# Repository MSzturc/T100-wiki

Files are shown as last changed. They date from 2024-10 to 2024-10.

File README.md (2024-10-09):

<p align="center">
  <a href="https://getdoks.org/">
    Doks
  </a>
</p>

<h1 align="center">
  Doks
</h1>

<h3 align="center">
  Modern Documentation Theme
</h3>

<p align="center">
  Doks is a Hugo theme for building secure, fast, and SEO-ready documentation websites, which you can easily update and customize.
</p>

<p align="center">
  <a href="https://github.com/h-enk/doks/blob/master/LICENSE">
    
  </a>
  <a href="https://github.com/h-enk/doks/releases">
    
  </a>
  <a href="https://www.npmjs.com/package/@hyas/doks">
    
  </a>
  <a href="https://github.com/h-enk/doks/actions?query=workflow%3A%22Hyas+CI%22">
    
  </a>
  <a href="https://app.netlify.com/sites/doks/deploys">
    
  </a>
</p>

Doks — Modern Documentation Theme

## Demo

- [doks.netlify.app](https://doks.netlify.app/)

## Why Doks?

Nine main reasons why you should use Doks:

1. __Security aware__. Get A+ scores on [Mozilla Observatory](https://observatory.mozilla.org/analyze/doks.netlify.app) out of the box. Easily change the default Security Headers to suit your needs.

2. __Fast by default__. Get 100 scores on [Google Lighthouse](https://googlechrome.github.io/lighthouse/viewer/?gist=59aafe464a68f8bc30b8e9a636d5b053) by default. Doks removes unused css, prefetches links, and lazy loads images.

3. __SEO-ready__. Use sensible defaults for structured data, open graph, and Twitter cards. Or easily change the SEO settings to your liking.

4. __Development tools__. Code with confidence. Check styles, scripts, and markdown for errors and fix automatically or manually.

5. __Bootstrap framework__. Build robust, flexible, and intuitive websites with Bootstrap 5. Easily customize your Doks site with the source Sass files.

6. __Netlify-ready__. Deploy to Netlify with sensible defaults. Easily use Netlify Functions, Netlify Redirects, and Netlify Headers.

7. __Full text search__. Search your Doks site with FlexSearch. Easily customize index settings and search options to your liking.

8. __Page layouts__. Build pages with a landing page, blog, or documentation layout. Add custom sections and components to suit your needs.

9. __Dark mode__. Switch to a low-light UI with the click of a button. Change colors with variables to match your branding.

### Other features

- __Multilingual and i18n__ support
- __Versioning__ documentation support
- __KaTeX__ math typesetting
- __Mermaid__ diagrams and visualization
- __highlight.js__ syntax highlighting

## Requirements

- [Git](https://git-scm.com/) — latest source release
- [Node.js](https://nodejs.org/) — latest LTS version or newer

<details>
<summary>Why Node.js?</summary>

Doks uses npm (included with Node.js) to centralize dependency management, making it [easy to update](https://getdoks.org/docs/help/how-to-update/) resources, build tooling, plugins, and build scripts.

</details>

## Get started

Start a new Doks project in three steps:

### 1. Create a new site

Doks is available as a child theme and a starter theme.

#### Child theme

- Intended for novice to intermediate users
- Intended for minor customizations
- [Easily update npm packages](https://getdoks.org/docs/help/how-to-update/) — __including__ [Doks](https://www.npmjs.com/package/@hyas/doks)

```bash
git clone https://github.com/h-enk/doks-child-theme.git my-doks-site && cd my-doks-site
```

#### Starter theme

- Intended for intermediate to advanced users
- Intended for major customizations
- [Easily update npm packages](https://getdoks.org/docs/help/how-to-update/)

```bash
git clone https://github.com/h-enk/doks.git my-doks-site && cd my-doks-site
```

<details>
<summary>Help me choose</summary>

Not sure which one is for you? Pick the child theme.

</details>

### 2. Install dependencies

```bash
npm install
```

### 3. Start development server

```bash
npm run start
```

## Other commands

Doks comes with [commands](https://getdoks.org/docs/prologue/commands/) for common tasks.

## Documentation

- [Netlify](https://docs.netlify.com/)
- [Hugo](https://gohugo.io/documentation/)
- [Doks](https://getdoks.org/)

## Communities

- [Netlify Community](https://community.netlify.com/)
- [Hugo Forums](https://discourse.gohugo.io/)
- [Doks Discussions](https://github.com/h-enk/doks/discussions)

## Sponsors

Support this project by becoming a sponsor. Your logo will show up here with a link to your website.

OC sponsor 0 (https://opencollective.com/doks/tiers/sponsor/0/website)
OC sponsor 1 (https://opencollective.com/doks/tiers/sponsor/1/website)

## Backers

Support this project by becoming a backer. Your avatar will show up here.

Backers (https://opencollective.com/doks)

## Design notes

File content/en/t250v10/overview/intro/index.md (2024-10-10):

---
title: "Intro"
description: "Welcome to a print and build how to guide for the T250 v1.0 3d printer!"
lead: ""
date: 2023-06-18T14:41:39+01:00
draft: false
images: []
type: docs
menu:
  t250v10:
    parent: "overview-t250-v11"
    identifier: "intro-t250-v11"
weight: 50
toc: true
doc: t250v10
static_images: true
images: 
---
# T250 3d Printer

## Welcome!

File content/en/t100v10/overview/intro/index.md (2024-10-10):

---
title: "Intro"
description: "Welcome to a print and build how to guide for THE 100 3d printer!"
lead: ""
date: 2023-06-18T14:41:39+01:00
lastmod: 2023-06-21T00:41:39+01:00
draft: false
images: []
type: docs
menu:
  t100v10:
    parent: "overview-v10"
    identifier: "intro-v10"
weight: 50
toc: true
doc: t100v10
aliases:
  - /t100/overview/intro/
  - /t100/overview/
---
# THE 100 3d Printer

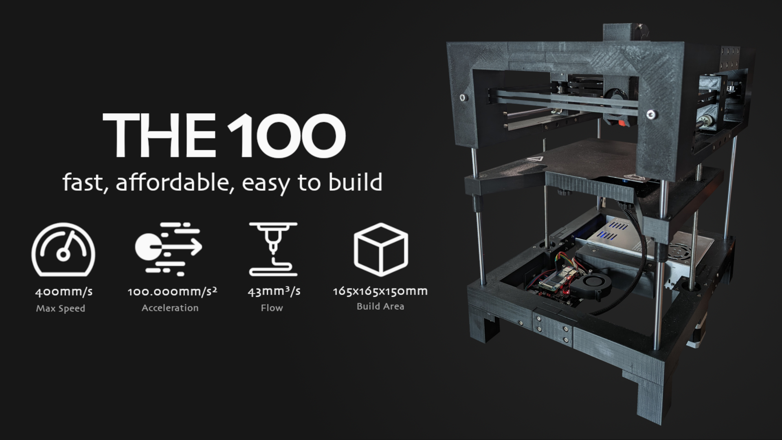
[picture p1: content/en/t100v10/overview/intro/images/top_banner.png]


## Welcome!
If you found this page then you probably already know what THE 100 project is, but just in case you don't: it's a 3d printable 3d printer designed by <a href="https://github.com/MSzturc">Matt</a>. 

Matt himself has created a <a href="https://www.youtube.com/watch?v=fC4BB4BhjOo&list=PLM01o_dfwbDcKYB-9yV0vLs5k0CrHUv0W&pp=iAQB">great assembly guide on YouTube</a> but those videos don't go in to detail about how to actually print the parts. I struggled with knowing how many of each part to print and which parts I actually needed. As I've spent more time in THE 100 discord, I've seen these same questions come up often. 

Matt is working hard on v1.1 which has a number of changed parts (see <a href="/t100/overview/before-you-print/#warning">this warning</a> before you start printing), and he already said v2 is going to be a pretty massive design change, so the confusion around what to print for different versions is only going to make it harder for people to know where to start.

That inspired me to create this guide. It helps me remember it for future prints, and it will hopefully be helpful for others as well.

{{< alert icon="⛔" context="warning" text="This guide for THE 100 v1.0 is now considered complete aside from correcting any issues that are found. I am switching focus to working on v1.1 which will be a more thorough guide." />}}

## What is this guide for?
This guide is meant to answer questions about THE 100 like:

  * How many of each part do I need?
  * How many screws do I need of each size? How many heat inserts? And how many nuts?
  * How do the GitHub stls compare with the Printables stls?
  * How much filament does each piece need?
  * Mistakes to avoid
  * And a lot more

Now you may be wondering: <a href="/t100/1.0/overview/why-print-the-100/">why should I even print one of these</a>?

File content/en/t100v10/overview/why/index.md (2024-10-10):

---
title: "Why print THE 100?"
description: "Why should you build THE 100 3d printer?"
lead: ""
date: 2023-06-18T14:41:39+01:00
lastmod: 2023-06-21T00:41:39+01:00
draft: false
images: []
type: docs
menu:
  t100v10:
    parent: "overview-v10"
    identifier: "why-print-v10"
weight: 60
toc: true
doc: t100v10
aliases:
  - /t100/overview/why-print-the-100/
---
# Why print THE 100?
For me, 3d printing is purely a hobby. 50% of the fun for me is tweaking it. I could go out right now and buy a Bambu and get some incredible prints, but the lack of playing and tweaking isn't what I'm looking for. THE 100 is kind of the opposite of that: you have to build it yourself and you are solely responsible for making it work. And the reward when you do that successfully is you end up with the world's fastest 3d printer based on a printed frame. 

There are a lot of reasons to make this project, regardless of if you're newer to 3d printing or you're an advanced user:

  * You're interested in building a CoreXY-style printing but don't have $1000+ to spend on building a Voron or RatRig.
  * The idea of 3d printing a 3d printer just sounds fun to you. Even better that the entire thing is open source and can be built for ~$350.
  * Learn how to 3d print. Plain and simple. There are so many different parts that have different requirements to print, it's like jumping in to the deep end to learn how to swim. But don't let that scare you. Despite the complexity of the project, it's honestly very easy to do. 
  * Tweak and tune your current printer to get the best out of it.
  * Figure out exactly what your printer is capable of. How good of a print can it make? When do you need to use supports? 
  * Learn how to use a slicer beyond the defaults. Modify your profiles and determine the best setup for your printer.

Sound good to you? Let's move on then! Here are things you should know <a href="/t100/1.0/overview/before-you-print">before you print</a>.

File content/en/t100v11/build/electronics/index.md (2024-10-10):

---
title: "Electronics build"
ogTitle: "Electronics Build - THE 100 Build Guide"
description: "How to build THE 100's v1.1 electrical"
lead: ""
date: 2023-08-14T14:41:39+01:00
draft: true
images: []
type: docs
menu:
  t100v11:
    parent: "build-v11"
weight: 550
toc: true
doc: t100v11
images: 
  - images/tfd_toolhead_preview.png
---
# Toolhead

The toolhead is the "business end" of the printer and is also the first part we're going to build. 

Visit the <a href="/t100/1.1/printing-guide/toolhead/">print & purchase guide for the toolhead</a> to see what parts you will need to complete this part of the build. 

Then you should watch <a href="https://www.youtube.com/watch?v=fC4BB4BhjOo" target="_blank">Matt's video</a> for building the toolhead. This guide will simply function as a supplement to that video. 

## Notes on the video

The build video for the toolhead is great and covers all steps well. 

## Tips

  - There are various qualities of drylins, and how they work with your linear rods will vary. I bought some that were so tight I could barely move them, and others that were super smooth but a bit loose. In the end I actually switched from drylins to linear bearings as I didn't mind the sound difference and they just worked better for me. 
  - A nice step to prep your linear rods is to clean them off with alcohol and then use melamine foam (aka magic eraser) and give it a nice quick buff, followed by another wipe down with alcohol. I could barely tell any difference in how smooth the rod was, but I immediately had smoother movements after doing this to all my linear rods. 
  - If you haven't built a hot end before (heatsink + heat break + nozzle + nozzle adapter in some cases) then you may run in to issues like I did. It seems like a straightforward process but because I screwed the heat break in first, my nozzle ended up sticking out too far. I didn't realize something was wrong or that this was a problem until I kept getting clogs. This was caused by the heater being too far away from the nozzle. I would suggest putting the nozzle in first so you can get it to the right position (slightly below, <a href="https://ueeshop.ly200-cdn.com/u_file/UPAT/UPAT086/2205/04/products/4-e8fa.jpg" target="_blank">but not actually touching</a>, the ceramic heater), then the heatbreak and heatsink. Once you put the orange silicone sock on, <a href="https://ueeshop.ly200-cdn.com/u_file/UPAT/UPAT086/2205/04/products/5-6820.jpg">the sock should be wrapped around the hex-shape of the nozzle with just the cone shaped tip coming out</a>. If have a lot more sticking out then your nozzle is probably too low. It should go without saying but you need to make sure the heat break is screwed in enough to touch the nozzle. 
  - Don't expect this to be the last time you build the toolhead. It will need taken apart to change nozzles, to deal with clogs, to replace your ptfe tube, etc, etc. I think I probably took mine apart at least 10-15 times during the tuning phase. It's annoying at first, but you get faster at it and then it starts to feel like a Formula 1 pit stop.

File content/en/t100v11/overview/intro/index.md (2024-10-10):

---
title: "Intro"
description: "Welcome to a print and build how to guide for THE 100 v1.1 3d printer!"
lead: ""
date: 2023-06-18T14:41:39+01:00
draft: false
images: []
type: docs
menu:
  t100v11:
    parent: "overview-v11"
    identifier: "intro-v11"
weight: 50
toc: true
doc: t100v11
static_images: true
images: 
  - tfd_the100_preview.png
---
# THE 100 3d Printer



## Welcome!
If you found this page then you probably already know what THE 100 project is, but just in case you don't: it's a 3d printable 3d printer designed by <a href="https://github.com/MSzturc">Matt</a>. 

Matt himself has created a <a href="https://www.youtube.com/watch?v=fC4BB4BhjOo&list=PLM01o_dfwbDcKYB-9yV0vLs5k0CrHUv0W&pp=iAQB">great assembly guide on YouTube</a> but those videos don't go in to detail about how to actually print the parts. I struggled with knowing how many of each part to print and which parts I actually needed. As I've spent more time in THE 100 discord, I've seen these same questions come up often. 

## What is this guide for?
This guide is meant to answer questions about THE 100 like:

  * How many of each part do I need?
  * How many screws do I need of each size? How many heat inserts? And how many nuts?
  * How much filament does each piece need?
  * Mistakes to avoid
  * How do I build it?
  * How to I configure it?
  * And a lot more

Now you may be wondering: <a href="/t100/1.1/overview/why-print-the-100/">why should I even print one of these</a>?

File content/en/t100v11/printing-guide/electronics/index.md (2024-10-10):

---
title: "Electronics"
ogTitle: "Electronics - THE 100 Print Guide"
description: "How to print THE 100's v1.1 electronic components, as well as what hardware you need to purchase to build it."
lead: ""
date: 2023-06-18T14:41:39+01:00
draft: false
images: []
type: docs
menu:
  t100v11:
    parent: "printing-guide-the100"
weight: 450
toc: true
doc: t100v11
images: 
  - images/tfd_electronics_preview.png
---
# Electronics
Everything you need to print to hold THE 100's electronics. You can't print the electronics themselves... yet. 

<div class="row bd">
  <div class="col">
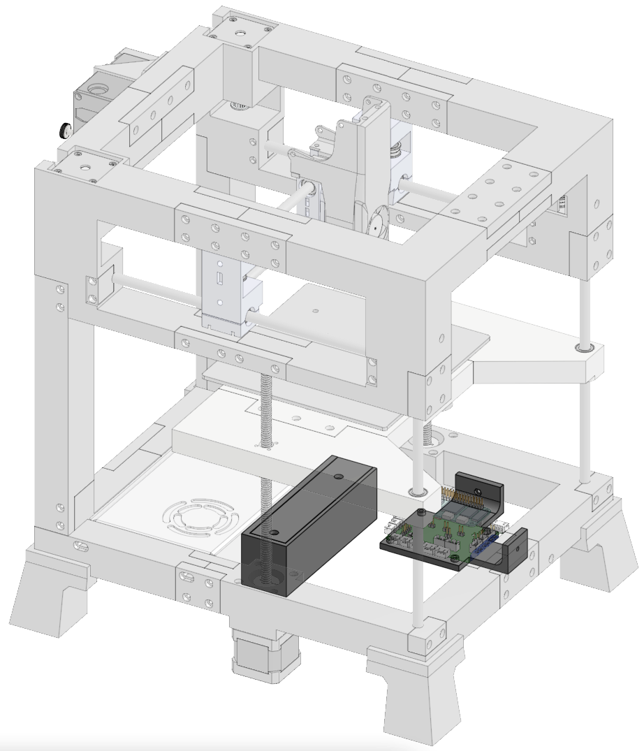
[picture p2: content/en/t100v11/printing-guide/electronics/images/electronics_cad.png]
      
  </div>
  <div class="col">
    <ul class="list-group">
      <li class="list-group-item d-flex justify-content-between align-items-center">
        <div class="text fw-bold">Printed parts</div>
        <div class="text">6</div>
      </li>
    </ul>
    <br>
    <ul class="list-group">
      <li class="list-group-item d-flex justify-content-between align-items-center">
        <div class="text fw-bold">Purchased parts</div>
        <div class="text">28</div>
      </li>
    </ul>   
    <br>
    <ul class="list-group">
      <li class="list-group-item d-flex justify-content-between align-items-center">
        <div class="text fw-bold">Filament</div>
        <div class="text">46.8m | 119.7g</div>
      </li>
    </ul>   
    <br>
    <ul class="list-group">
      <li class="list-group-item d-flex justify-content-between align-items-center">
        <div class="text fw-bold">Print time</div>
        <div class="text">7h 54m</div>
      </li>
    </ul>  
  </div>
</div>

### Printed parts
<table class="table table-sm">
  <thead>
    <tr>
      <th scope="col">Part Name</th>
      <th scope="col">STL</th>
      <th scope="col">Qty</th>
      <th scope="col">Notes</th>
    </tr>
  </thead>
  <tbody>
    <tr>
      <td>Cable Holder Frame</td>
      <td class="no-wrap"><a target="_blank" href="https://github.com/MSzturc/t100/blob/main/STL/Electronics/Cable%20Holder%20Frame.stl">github</a> / <a href="https://files.printables.com/media/prints/572689/stls/4581556_19129328-4335-465a-b671-f0bd2a63f9c6/cable-holder-frame.stl">printables</a></td>
      <td>1</td>
      <td><a href="#cable-holder-frame">More info</a></td>
    </tr>
    <tr>
      <td>Cable Holder Top</td>
      <td class="no-wrap"><a target="_blank" href="https://github.com/MSzturc/t100/blob/main/STL/Electronics/Cable%20Holder%20Top.stl">github</a> / <a href="https://files.printables.com/media/prints/572689/stls/4581557_c0b56564-be73-4338-9c44-279b15b9c600/cable-holder-top.stl">printables</a></td>
      <td>1</td>
      <td><a href="#cable-holder-top">More info</a></td>
    </tr>
    <tr>
      <td>Mainboard Holder</td>
      <td class="no-wrap"><a target="_blank" href="https://github.com/MSzturc/t100/blob/main/STL/Electronics/Mainboard%20Holder.stl">github</a> / <a href="https://files.printables.com/media/prints/572689/stls/4581558_7a9a4bd0-a8d6-4a6c-910a-24303c0e0896/mainboard-holder.stl">printables</a></td>
      <td>1</td>
      <td><a href="#mainboard-holder">More info</a></td>
    </tr>
  </tbody>
</table>

### Purchased Parts
<table class="table table-sm no-margin">
  <thead>
    <tr>
      <th scope="col">Item</th>
      <th scope="col">Qty</th>
      <th scope="col">Notes</th>
    </tr>
  </thead>
  <tbody>
    <tr>
      <td>m3 heat inserts</td>
      <td>2</td>
      <td></td>
    </tr>
    <tr>
      <td>m2.5x40 screw</td>
      <td>4</td>
      <td></td>
    </tr>
    <tr>
      <td>m2.5 nut</td>
      <td>12</td>
      <td></td>
    </tr>
    <tr>
      <td>m3x6 screw</td>
      <td>2</td>
      <td></td>
    </tr>
    <tr>
      <td>m3 nut</td>
      <td>2</td>
      <td></td>
    </tr>
  </tbody>
</table>

### Details

#### Cable Holder Frame
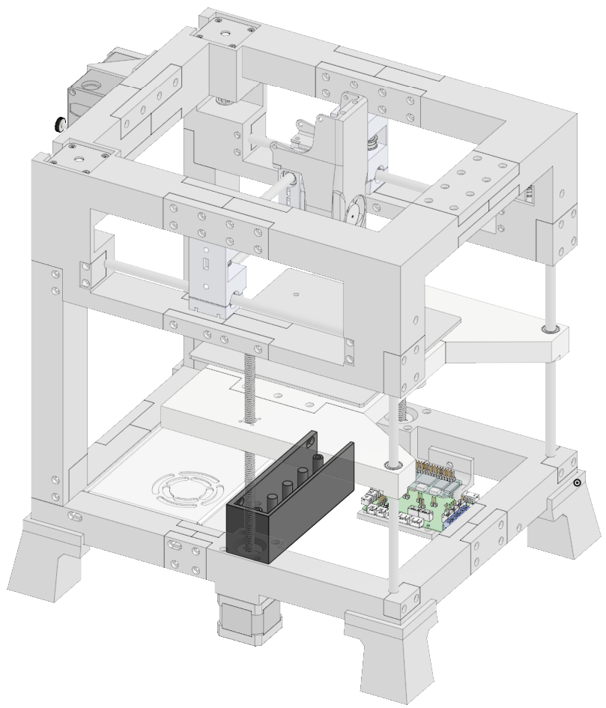
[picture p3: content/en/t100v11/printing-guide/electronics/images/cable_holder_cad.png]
  
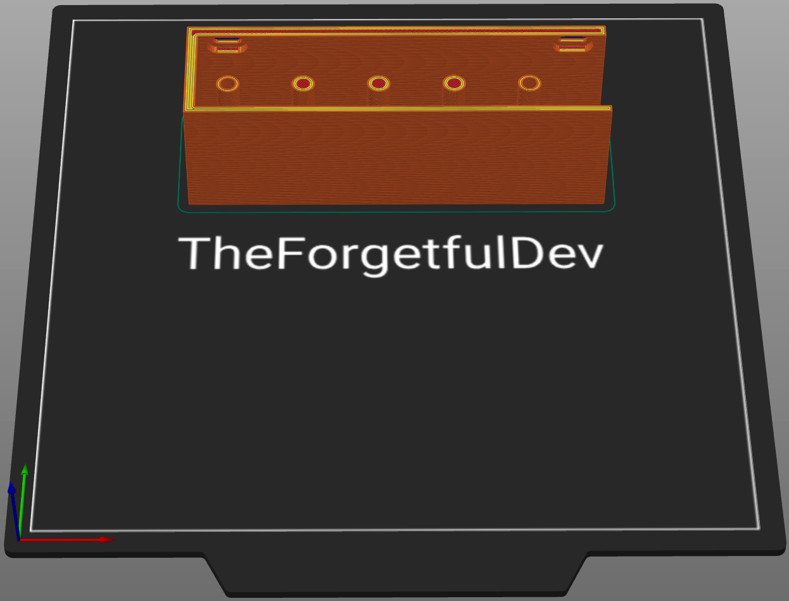
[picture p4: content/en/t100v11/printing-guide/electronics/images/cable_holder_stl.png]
  
##### Print
<table class="table table-striped table-hover no-margin">
  <tbody class="table-group-divider">
    <tr>
      <th scope="row" class="no-wrap">Quantity</th>
      <td> </td>
      <td>1</td>
    </tr>
    <tr>
      <th scope="row" class="no-wrap">Filament Length</th>
      <td> </td>
      <td>28m</td>
    </tr>
    <tr>
      <th scope="row" class="no-wrap">Filament Weight</th>
      <td> </td>
      <td>63.6g</td>
    </tr>
    <tr>
      <th scope="row" class="no-wrap">Supports?</th>
      <td> </td>
      <td>No</td>
    </tr>
  </tbody>
</table>

##### Purchase
<table class="table table-striped table-hover no-margin">
  <thead>
    <tr>
      <th scope="col">Item</th>
      <th scope="col">Qty</th>
      <th scope="col">Note</th>
    </tr>
  </thead>
  <tbody>
    <tr>
      <td>m3 heat inserts</td>
      <td>2</td>
      <td></td>
    </tr>
  </tbody>
</table>

#### Cable Holder Top
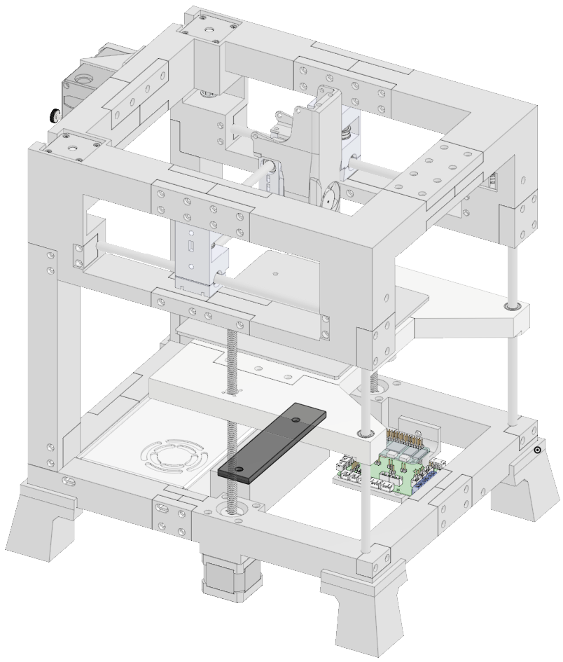
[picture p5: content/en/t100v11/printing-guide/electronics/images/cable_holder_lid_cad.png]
  
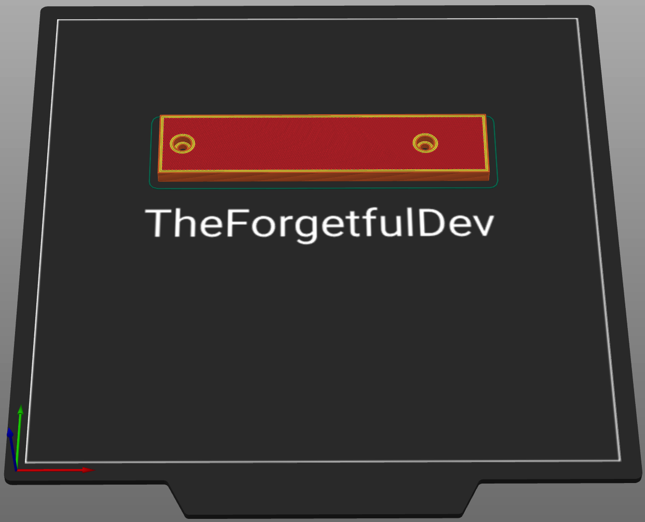
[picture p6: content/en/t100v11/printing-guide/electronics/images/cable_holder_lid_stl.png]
  
##### Print
<table class="table table-striped table-hover no-margin">
  <tbody class="table-group-divider">
    <tr>
      <th scope="row" class="no-wrap">Quantity</th>
      <td> </td>
      <td>1</td>
    </tr>
    <tr>
      <th scope="row" class="no-wrap">Filament Length</th>
      <td> </td>
      <td>5.9m</td>
    </tr>
    <tr>
      <th scope="row" class="no-wrap">Filament Weight</th>
      <td> </td>
      <td>17.7g</td>
    </tr>
    <tr>
      <th scope="row" class="no-wrap">Supports?</th>
      <td> </td>
      <td>No</td>
    </tr>
  </tbody>
</table>

##### Purchase
<table class="table table-striped table-hover no-margin">
  <thead>
    <tr>
      <th scope="col">Item</th>
      <th scope="col">Qty</th>
      <th scope="col">Note</th>
    </tr>
  </thead>
  <tbody>
    <tr>
      <td>m3x6 screw</td>
      <td>2</td>
      <td></td>
    </tr>
  </tbody>
</table>

#### Mainboard Holder
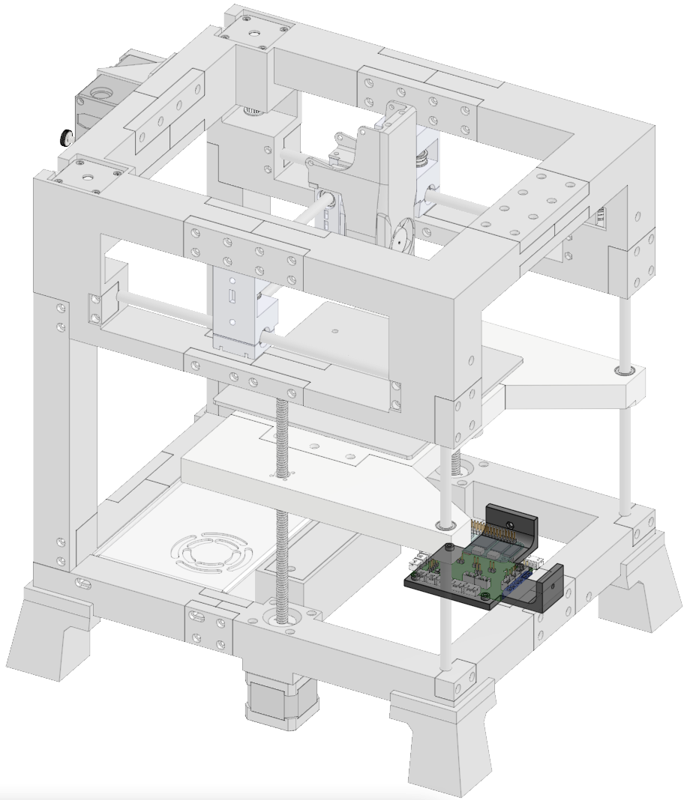
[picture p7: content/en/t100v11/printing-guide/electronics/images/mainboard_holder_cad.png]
  
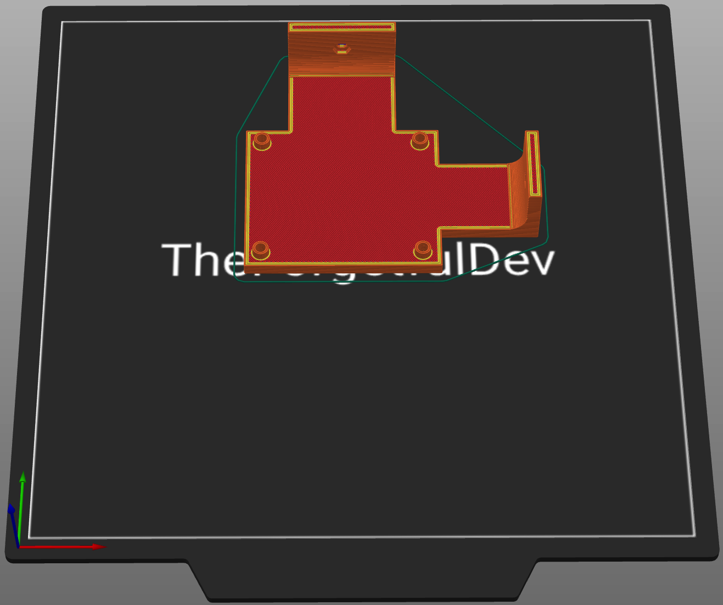
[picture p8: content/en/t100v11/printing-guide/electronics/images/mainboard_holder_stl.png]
  
##### Print
<table class="table table-striped table-hover no-margin">
  <tbody class="table-group-divider">
    <tr>
      <th scope="row" class="no-wrap">Quantity</th>
      <td> </td>
      <td>1</td>
    </tr>
    <tr>
      <th scope="row" class="no-wrap">Filament Length</th>
      <td> </td>
      <td>11m</td>
    </tr>
    <tr>
      <th scope="row" class="no-wrap">Filament Weight</th>
      <td> </td>
      <td>32.8g</td>
    </tr>
    <tr>
      <th scope="row" class="no-wrap">Supports?</th>
      <td> </td>
      <td>Yes - only in countersunk holes touching the buildplate</td>
    </tr>
  </tbody>
</table>

##### Purchase
<table class="table table-striped table-hover no-margin">
  <thead>
    <tr>
      <th scope="col">Item</th>
      <th scope="col">Qty</th>
      <th scope="col">Note</th>
    </tr>
  </thead>
  <tbody>
    <tr>
      <td>m2.5x40 screw</td>
      <td>4</td>
      <td>Optional. Just my custom solution for stacking.</td>
    </tr>
    <tr>
      <td>m2.5 nut</td>
      <td>12</td>
      <td>Optional. Just my custom solution for stacking.</td>
    </tr>
    <tr>
      <td>m3 nuts</td>
      <td>2</td>
      <td></td>
    </tr>
  </tbody>
</table>

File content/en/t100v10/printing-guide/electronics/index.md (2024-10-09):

---
title: "Electronics"
description: ""
lead: ""
date: 2023-06-18T14:41:39+01:00
lastmod: 2023-06-21T00:41:39+01:00
draft: false
images: []
type: docs
menu:
  t100v10:
    parent: "printing-guide-the100"
weight: 360
toc: true
doc: t100v10
aliases:
  - /t100/printing-guide/electronics/
---
# Electronics
Everything you need to print for THE 100 electronics.

## v1.0

### Parts List - All

<table class="table table-sm">
  <thead>
    <tr>
      <th scope="col">GitHub</th>
      <th scope="col">Printables</th>
      <th scope="col">Qty</th>
      <th scope="col">Notes</th>
    </tr>
  </thead>
  <tbody>
    <tr>
      <td><a href="https://github.com/MSzturc/t100/blob/main/STL/Electronics/CableHolder.stl">CableHolder</a></td>
      <td><a href="https://files.printables.com/media/prints/430339/stls/3564398_d9bbaf82-8061-486f-846e-187a0d8403ab/cable-holder-top.stl">Cable Holder Top</a></td>
      <td>1</td>
      <td><a href="#cable-holder">More info</a></td>
    </tr>
    <tr>
      <td><a href="https://github.com/MSzturc/t100/blob/main/STL/Electronics/CableHolderTop.stl">CableHolderTop</a></td>
      <td><a href="https://files.printables.com/media/prints/430339/stls/3564395_ae9a1a7a-de9d-4b92-918b-68323fd70c03/cable-holder-frame.stl">Cable Holder Frame</a></td>
      <td>1</td>
      <td><a href="#cable-holder-top">More info</a></td>
    </tr>
    <tr>
      <td><a href="https://github.com/MSzturc/t100/blob/main/STL/Electronics/MainboardHolder.stl">MainboardHolder</a></td>
      <td><a href="https://files.printables.com/media/prints/430339/stls/3564387_aba3401a-202d-4cc9-8165-8f92b87a6177/mainboard-holder.stl">Mainboard Holder</a></td>
      <td>1</td>
      <td><a href="#mainboard-holder">More info</a></td>
    </tr>
    <tr>
      <td><a href="https://github.com/MSzturc/t100/blob/main/STL/Electronics/Spacer15mm.stl">Spacer15mm</a></td>
      <td><a href="https://files.printables.com/media/prints/430339/stls/3564394_7a06f0f7-ccd6-45a9-b77b-5a91f037212f/spacer-15mm.stl">Spacer 15mm</a></td>
      <td>4</td>
      <td><a href="#spacer-15mm">More info</a></td>
    </tr>
  </tbody>
</table>

### More Info

#### Cable Holder
##### Printing details
  - Qty: 1
  - Filament (length/weight): 28m / 83.5g
  - Supports: No

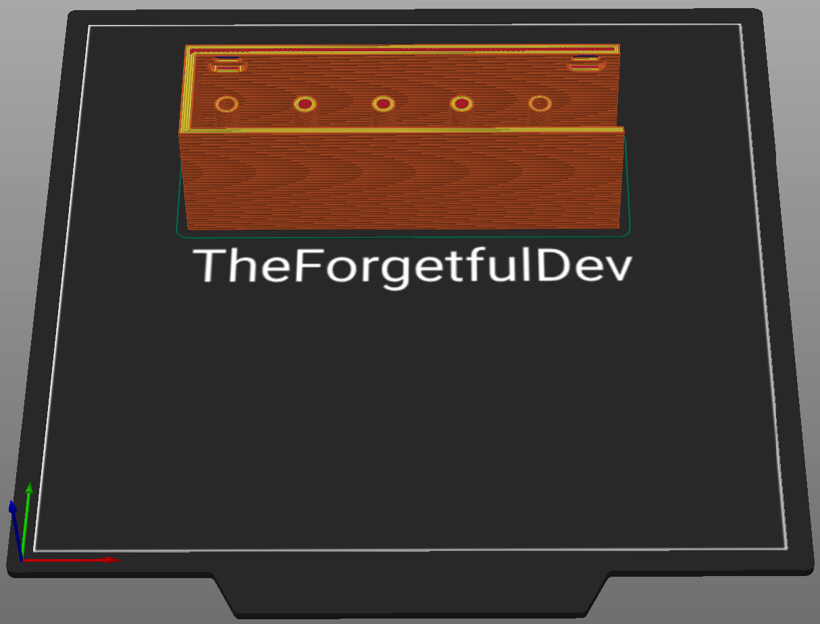
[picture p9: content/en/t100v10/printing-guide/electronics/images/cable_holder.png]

##### Notes
The upload on Printables has the name wrong. It says `Cable Holder Top` but is actually the cable holder itself. 

#### Cable Holder Top
##### Printing details
  - Qty: 1
  - Filament (length/weight): 5.9m / 17.7g
  - Supports: No

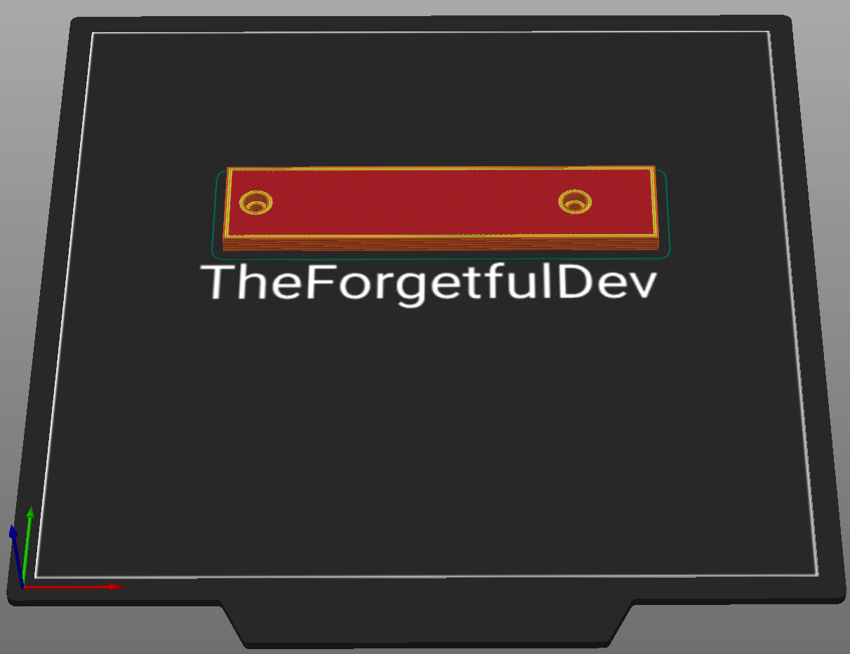
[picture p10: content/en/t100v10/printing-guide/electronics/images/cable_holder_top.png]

##### Notes
The upload on Printables has the name wrong. It says `Cable Holder Frame` but is actually the cable holder top. 

#### Mainboard Holder
##### Printing details
  - Qty: 1
  - Filament (length/weight): 11m / 32.8g
  - Supports: Yes - only in the countersunk holes that touch the build plate

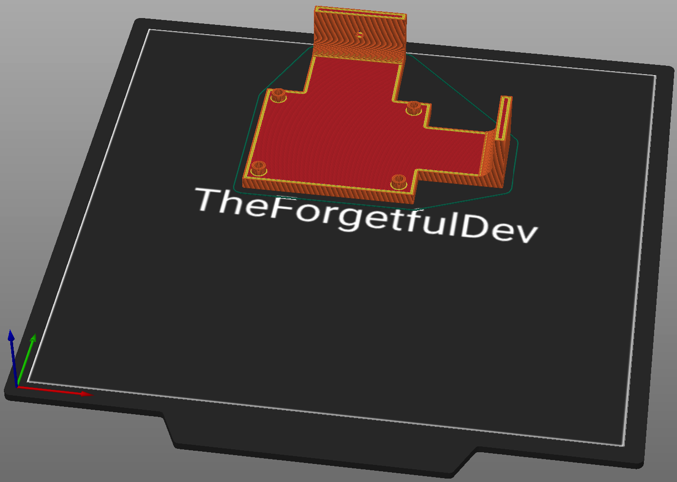
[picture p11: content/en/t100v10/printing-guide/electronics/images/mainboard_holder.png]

##### Notes
None

#### Spacer 15mm
##### Printing details
  - Qty: 2
  - Filament (length/weight): 0.1m / 0.4g
  - Supports: No

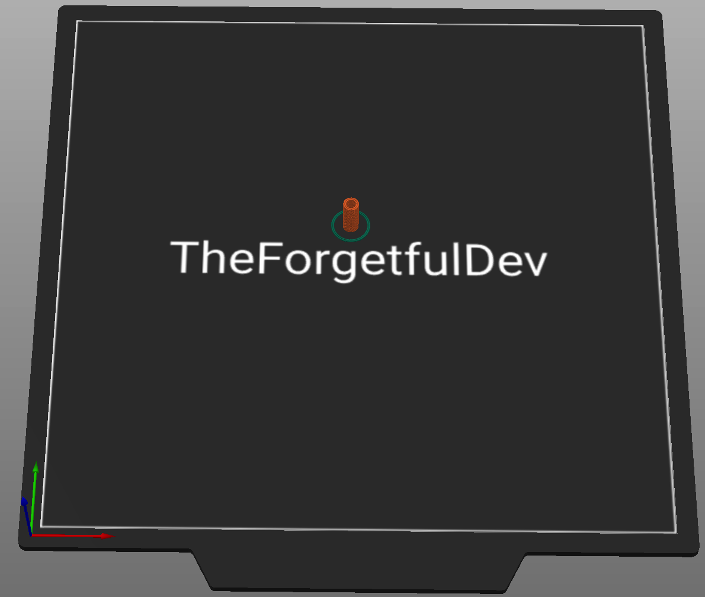
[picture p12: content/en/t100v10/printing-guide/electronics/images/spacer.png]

##### Notes
These can be used to create a space between the skr pico and the banana pi zero. They may not be necessary depending on how you setup your electronics stack.

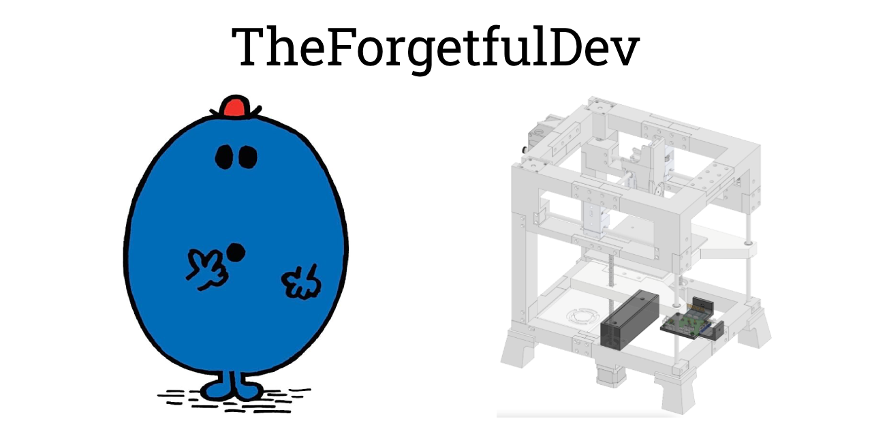
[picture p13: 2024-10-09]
content/en/t100v11/printing-guide/electronics/images/tfd_electronics_preview.png

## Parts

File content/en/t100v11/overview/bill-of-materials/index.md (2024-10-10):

---
title: "Bill of Materials"
ogTitle: "BOM - THE 100 Build Guide"
description: "What to buy before you can build THE 100 v1.1 3d printer"
lead: ""
date: 2023-07-11T14:41:39+01:00
draft: false
images: []
type: docs
menu:
  t100v11:
    parent: "overview-v11"
    identifier: "bom-v11"
weight: 80
toc: true
doc: t100v11
images: 
  - images/tfd_bom_preview.png
---
# Bill of Materials

The printhead, frame, gantry, and more are all 3d printed parts. That's what makes this printer so awesome. But for obvious reasons there are still a number of items that need to be purchased. 

The official BOM is available <a href="https://docs.google.com/spreadsheets/d/1e5dhm4ck-dtci_GDkMuuwxgp788YJ5hdL6JvRKvF1Zc/edit#gid=0">here</a>. 

Some of the more expensive parts or more commonly asked about parts are (in no particular order):

  * Ender 2 Pro heated bed (yes, Ender 2. Not 3)
  * SKR Pico mainboard
  * Banana Pi M2 Zero
  * ~3KG of filament

I was able to purchase everything I needed off AliExpress. In the future I will post links to the companies I used but for now that's <a href="https://www.patreon.com/The100">a Patreon exclusive on Matt's Patreon</a> and I want to respect that.

## Warning
This entire guide is a major work-in-progress, but the BOM in particular is just now being started. Make sure you reference <a href="https://docs.google.com/spreadsheets/d/1e5dhm4ck-dtci_GDkMuuwxgp788YJ5hdL6JvRKvF1Zc/edit#gid=0">the official BOM</a> as well. The current revision of this guide is based on THE 100 v1.1-beta1. That means my counts for screws and heat inserts may be slightly off once v1.1-final is released. It should be very close though.

I will be updating this guide to reference v1.1-final once it is released.

## Fasteners / Hardware
Screw lengths can often be interchanged with one size up or down. For example you can almost always use an m3x10 where an m3x12 is called for. The sizes listed below are what I personally recommend, but you will find people using slightly different sizes in some cases. 

I have minimized different sizes as much as possible but I'd personally rather have the right size than to make something work. I will continue to minimize the different sizes if possible though.

### M2.5
ℹ️ M2.5 is only needed because the mounting holes on the BTT SKR Pico are M2.5. If you have another mounting solution, or you're willing to drill out the mounting holes on the board to fit M3, then you don't need these.
<div class="bd">
  <table class="table table-striped table-hover no-margin">
    <thead>
      <tr>
        <th scope="col">Item</th>
        <th scope="col" width="10%">Qty</th>
      </tr>
    </thead>
    <tbody>
      <tr> <td>m2.5 nut</td> <td>12</td> </tr>
      <tr> <td>m2.5x40 screw</td> <td>4</td> </tr>
    </tbody>
  </table>
</div>

### M3
M3-sized fasteners make up the vast majority of what is needed to build the printer. 
<div class="bd">
  <table class="table table-striped table-hover no-margin">
    <thead>
      <tr>
        <th scope="col">Item</th>
        <th scope="col" width="10%">Qty</th>
      </tr>
    </thead>
    <tbody>
      <tr> <td>m3 heat insert</td> <td>158</td> </tr>
      <tr> <td>m3 nut</td> <td>29</td> </tr>
      <tr> <td>m3 washer</td> <td>8</td> </tr>
      <tr> <td>m3x6 screw</td> <td>14</td> </tr>
      <tr> <td>m3x10 screw</td> <td>40</td> </tr>
      <tr> <td>m3x12 screw</td> <td>76</td> </tr>
      <tr> <td>m3x16 screw</td> <td>22</td> </tr>
      <tr> <td>m3x20 screw</td> <td>12</td> </tr>
      <tr> <td>m3x25 screw</td> <td>19</td> </tr>
      <tr> <td>m3x35 screw</td> <td>11</td> </tr>
      <tr> <td>m3x40 screw</td> <td>8</td> </tr>
    </tbody>
  </table>
</div>

### M5
M5-sized fasteners are primarily used for the belt-bearings to ride on. 
<div class="bd">
  <table class="table table-striped table-hover no-margin">
    <thead>
      <tr>
        <th scope="col">Item</th>
        <th scope="col" width="10%">Qty</th>
      </tr>
    </thead>
    <tbody>
      <tr> <td>m5 washer</td> <td>14</td> </tr>
      <tr> <td>m5x30 screw</td> <td>4</td> </tr>
      <tr> <td>m5x40 screw</td> <td>2</td> </tr>
    </tbody>
  </table>
</div>

## Filament
ℹ️ Weights are for PLA based on a density of 1.24 g/cm<sup>3</sup>.
<div class="bd">
  <table class="table table-striped table-hover no-margin">
    <thead>
      <tr>
        <th scope="col">Item</th>
        <th scope="col" width="30%">Qty</th>
      </tr>
    </thead>
    <tbody>
      <tr> <td>Single color</td> <td>3.4kg (3359g)</td> </tr>
      <tr> <td>-- OR --</td> <td></td> </tr>
      <tr> <td>Primary color (frame)</td> <td>1.7kg (1719g)</td> </tr>
      <tr> <td>Accent color (connectors)</td> <td>285g</td> </tr>
      <tr> <td>Other (use primary, accent, or other)</td> <td>1.4kg (1355g)</td> </tr>
    </tbody>
  </table>
</div>
<br><br>

##### Ordered everything you need?! <a href="/t100/1.1/printing-guide/toolhead/">Let's get printing</a>!

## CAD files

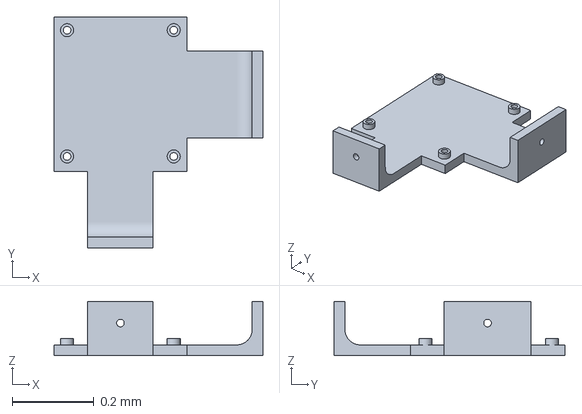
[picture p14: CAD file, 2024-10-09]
content/en/t100v11/build/electronics/models/3mf/mainboard_holder.3mf
0.512 x 0.565 x 0.133 mm

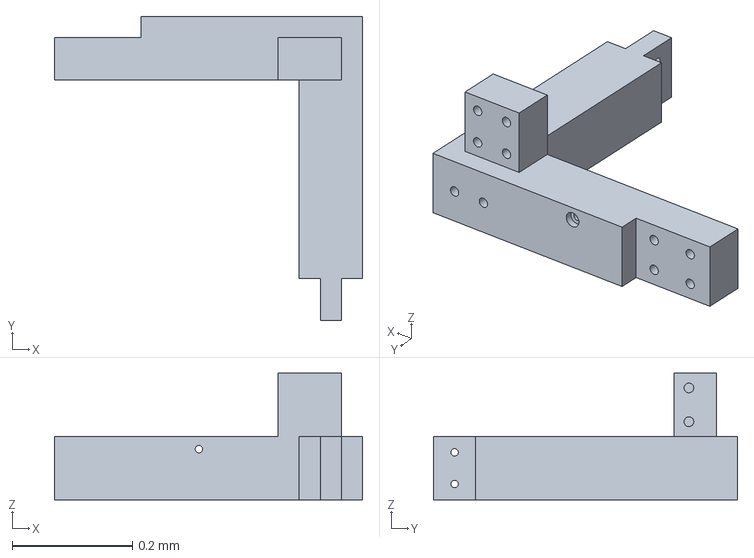
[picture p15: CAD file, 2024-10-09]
content/en/t100v11/build/bottom-frame-back-frame-bed/models/3mf/frame_back_right.3mf
0.512 x 0.505 x 0.211 mm

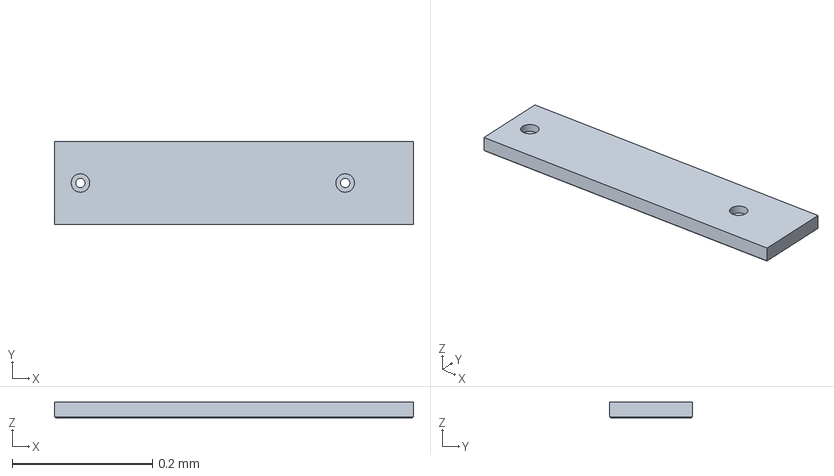
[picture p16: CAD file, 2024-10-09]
content/en/t100v11/build/electronics/models/3mf/cable_holder_lid.3mf
0.512 x 0.118 x 0.0227 mm

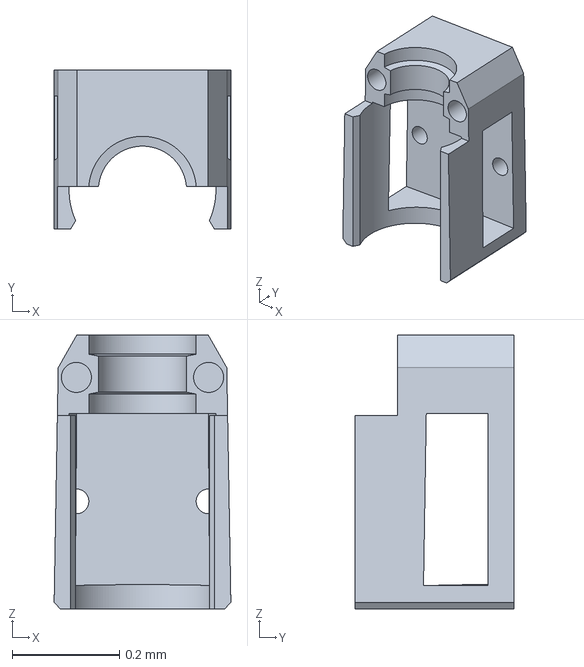
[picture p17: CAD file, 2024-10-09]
content/en/t100v11/build/toolhead/models/3mf/chc_pro_mount.3mf
0.33 x 0.298 x 0.512 mm

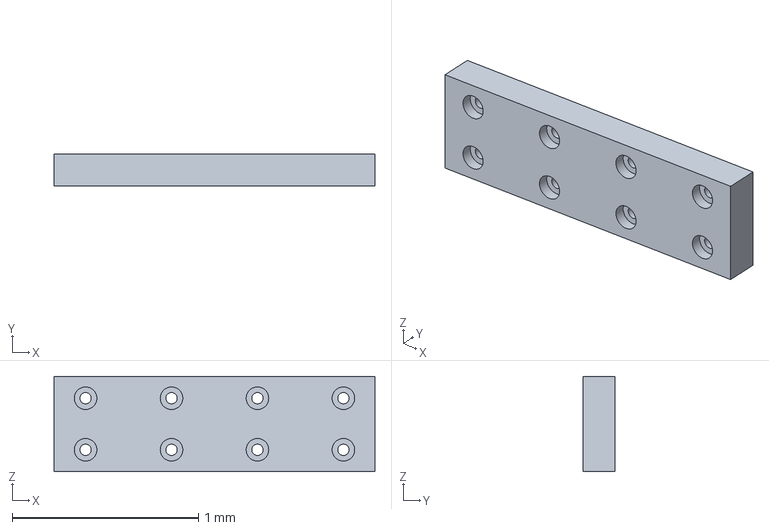
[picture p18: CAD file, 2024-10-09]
content/en/t100v11/build/top-frame-gantry/models/3mf/connector_side_1.3mf
1.72 x 0.173 x 0.512 mm

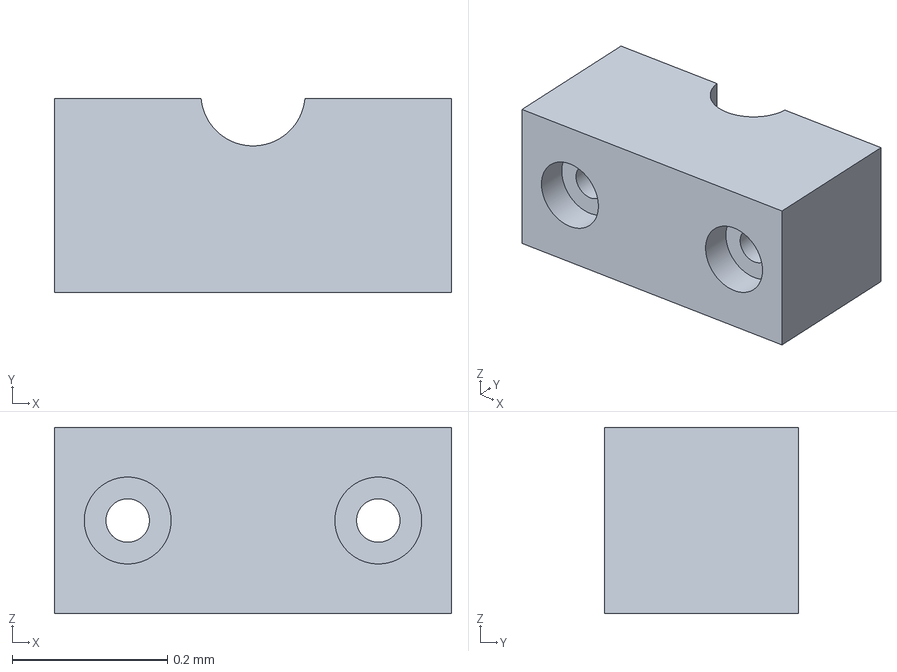
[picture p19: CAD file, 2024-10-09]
content/en/t100v11/build/bottom-frame-back-frame-bed/models/3mf/connector_z_rod.3mf
0.512 x 0.25 x 0.24 mm

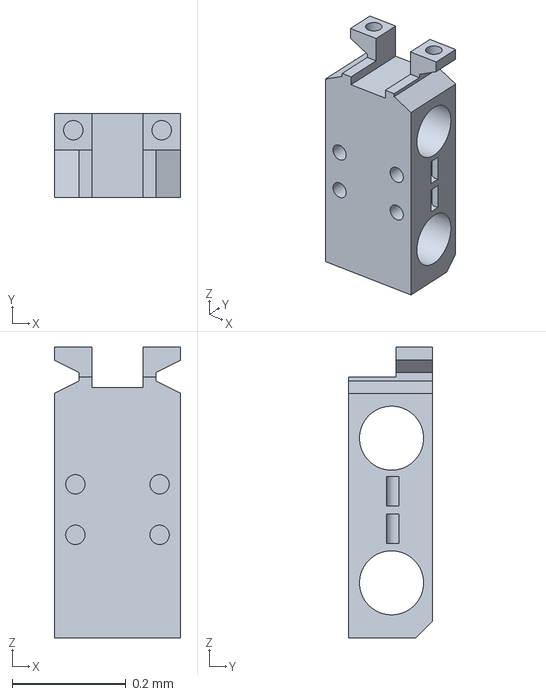
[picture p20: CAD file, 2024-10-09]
content/en/t100v11/build/toolhead/models/3mf/rod_cradle.3mf
0.222 x 0.148 x 0.512 mm

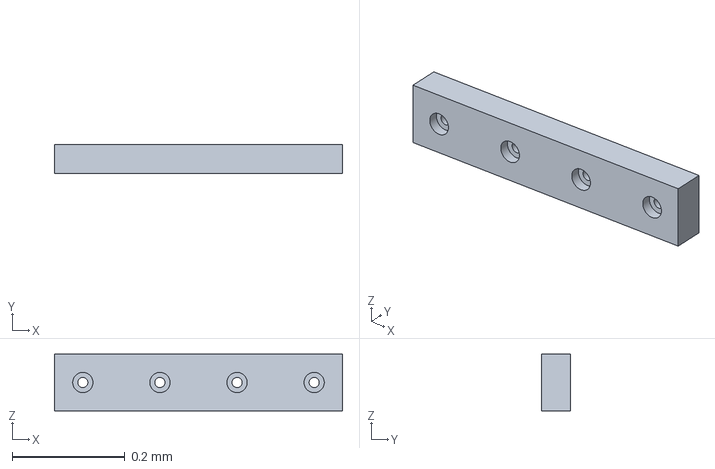
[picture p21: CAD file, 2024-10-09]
content/en/t100v11/build/top-frame-gantry/models/3mf/connector_back_1.3mf
0.512 x 0.0514 x 0.101 mm

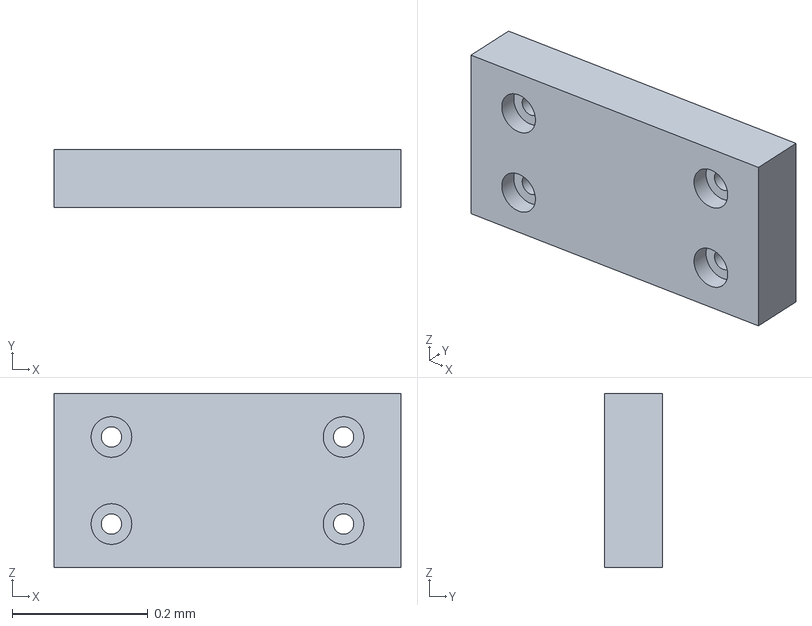
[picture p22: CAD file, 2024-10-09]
content/en/t100v11/build/bottom-frame-back-frame-bed/models/3mf/frame_connector_front_1.3mf
0.512 x 0.0856 x 0.257 mm

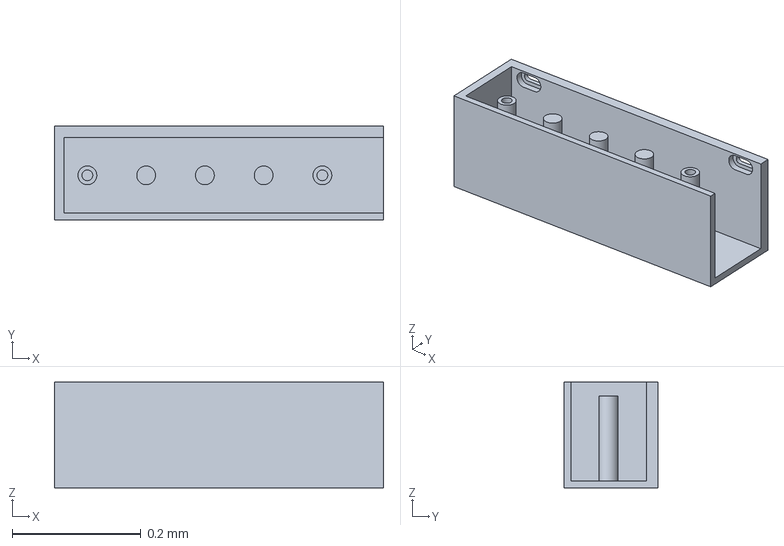
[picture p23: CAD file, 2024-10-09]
content/en/t100v11/build/electronics/models/3mf/cable_holder.3mf
0.512 x 0.146 x 0.165 mm

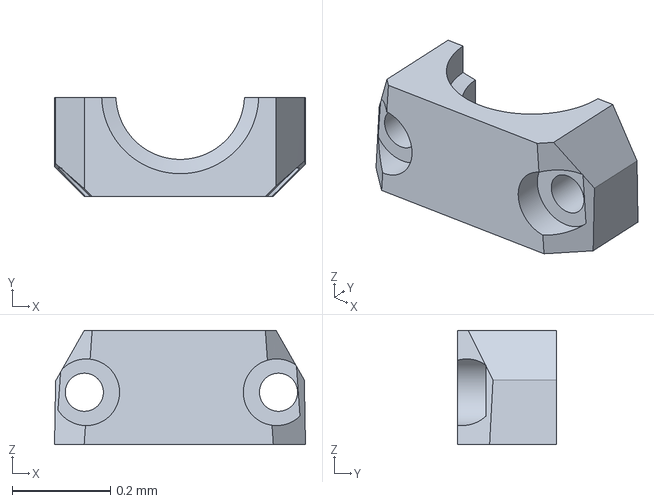
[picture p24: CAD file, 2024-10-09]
content/en/t100v11/build/toolhead/models/3mf/chc_pro_clamp.3mf
0.512 x 0.202 x 0.233 mm

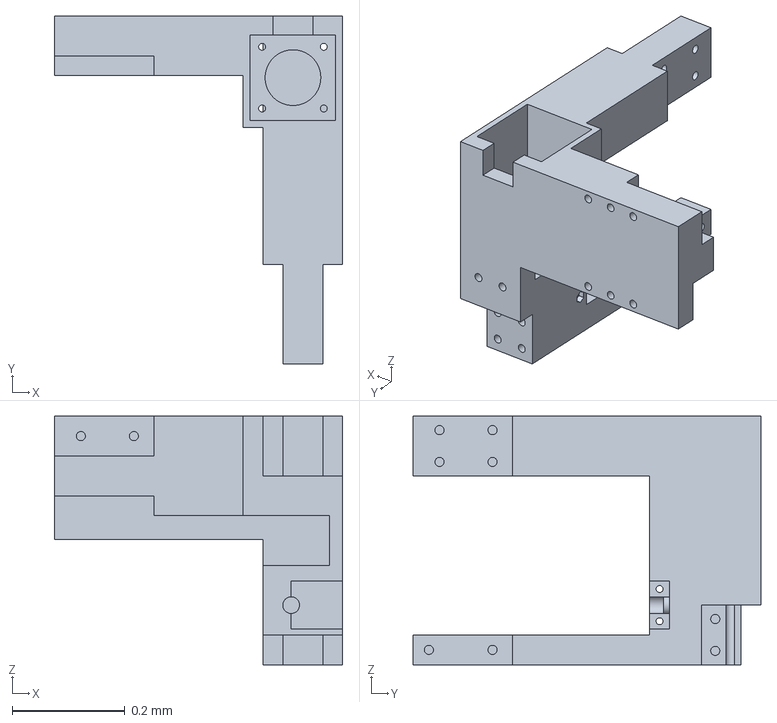
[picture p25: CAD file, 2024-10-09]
content/en/t100v11/build/top-frame-gantry/models/3mf/back_right.3mf
0.512 x 0.618 x 0.441 mm

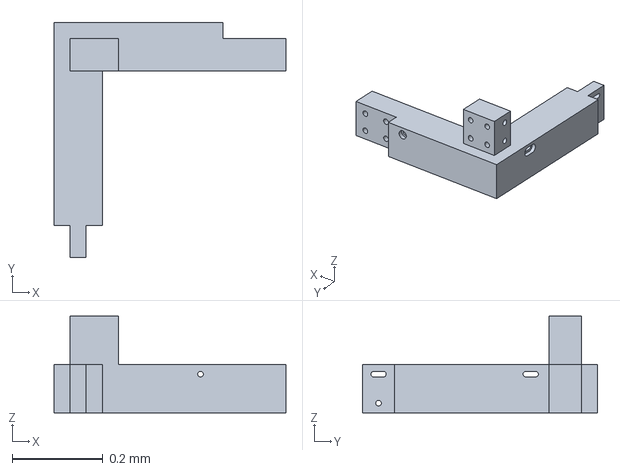
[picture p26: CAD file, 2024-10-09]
content/en/t100v11/build/bottom-frame-back-frame-bed/models/3mf/frame_back_left.3mf
0.512 x 0.519 x 0.213 mm

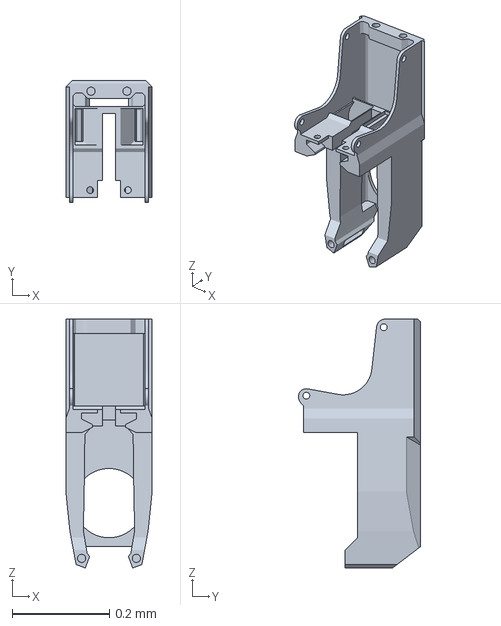
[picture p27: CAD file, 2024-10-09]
content/en/t100v11/build/toolhead/models/3mf/chc_pro_fanduct.3mf
0.178 x 0.251 x 0.512 mm

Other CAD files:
content/en/t100v11/build/top-frame-gantry/models/3mf/front_right.3mf
content/en/t100v11/build/bottom-frame-back-frame-bed/models/3mf/connector_back.3mf
content/en/t100v11/build/top-frame-gantry/models/3mf/connector_top_1.3mf
content/en/t100v11/build/bottom-frame-back-frame-bed/models/3mf/cable_guide_clamp.3mf
content/en/t100v11/build/bottom-frame-back-frame-bed/models/3mf/back_connector.3mf
content/en/t100v11/build/bottom-frame-back-frame-bed/models/3mf/foot_with_clamp.3mf
content/en/t100v11/build/bottom-frame-back-frame-bed/models/3mf/frame_connector_front_2.3mf
content/en/t100v11/build/bottom-frame-back-frame-bed/models/3mf/frame_connector_left_1.3mf
content/en/t100v11/build/bottom-frame-back-frame-bed/models/3mf/frame_connector_left_2.3mf
content/en/t100v11/build/bottom-frame-back-frame-bed/models/3mf/frame_connector_right_1.3mf
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

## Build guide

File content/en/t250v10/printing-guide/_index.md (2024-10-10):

---
title: "Print & Purchase"
description: ""
lead: ""
date: 2023-06-18T14:41:39+01:00
lastmod: 2023-06-21T00:41:39+01:00
draft: false
images: []
type: docs
weight: 200
url: /t250/1.0/printing-guide/
---

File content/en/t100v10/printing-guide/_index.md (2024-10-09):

---
title: "Printing"
description: ""
lead: ""
date: 2023-06-18T14:41:39+01:00
lastmod: 2023-06-21T00:41:39+01:00
draft: false
images: []
type: docs
weight: 200
url: /t100/1.0/printing-guide/
aliases:
  - /t100/printing-guide/
---

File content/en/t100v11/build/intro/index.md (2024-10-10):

---
title: "Intro"
ogTitle: "Build Intro - THE 100 Build Guide"
description: "How to build THE 100 v1.1"
lead: ""
date: 2023-08-14T14:41:39+01:00
draft: false
images: []
type: docs
menu:
  t100v11:
    parent: "build-v11"
weight: 501
toc: true
doc: t100v11
static_images: true
images: 
  - tfd_the100_preview.png
---
# Start your build
This guide is meant to be used as a supplement to Matt's excellent build videos on YouTube. 

He does a great job walking you through what is needed and I recommend watching each video a couple times before getting started. This guide -- at least in its current form -- is meant to provide additional clarification or details on steps in the videos. 

I will continue to update the build guide as additional questions come up from those that are building The 100. 

Ready to go? Let's build the toolhead!

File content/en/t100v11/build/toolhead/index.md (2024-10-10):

---
title: "Toolhead build"
ogTitle: "Toolhead Build - THE 100 Build Guide"
description: "How to build THE 100's v1.1 toolhead"
lead: ""
date: 2023-08-14T14:41:39+01:00
draft: false
images: []
type: docs
menu:
  t100v11:
    parent: "build-v11"
weight: 510
toc: true
doc: t100v11
images: 
  - images/tfd_toolhead_preview.png
---
# Toolhead

The toolhead is the "business end" of the printer and is also the first part we're going to build. 

Visit the <a href="/t100/1.1/printing-guide/toolhead/">print & purchase guide for the toolhead</a> to see what parts you will need to complete this part of the build. 

Then you should watch <a href="https://www.youtube.com/watch?v=fC4BB4BhjOo" target="_blank">Matt's video</a> for building the toolhead. This guide will simply function as a supplement to that video. 

## Notes on the video

The build video for the toolhead is great and covers all steps well. 

## Tips

  - There are various qualities of drylins, and how they work with your linear rods will vary. I bought some that were so tight I could barely move them, and others that were super smooth but a bit loose. In the end I actually switched from drylins to linear bearings as I didn't mind the sound difference and they just worked better for me. 
  - A nice step to prep your linear rods is to clean them off with alcohol and then use melamine foam (aka magic eraser) and give it a nice quick buff, followed by another wipe down with alcohol. I could barely tell any difference in how smooth the rod was, but I immediately had smoother movements after doing this to all my linear rods. 
  - If you haven't built a hot end before (heatsink + heat break + nozzle + nozzle adapter in some cases) then you may run in to issues like I did. It seems like a straightforward process but because I screwed the heat break in first, my nozzle ended up sticking out too far. I didn't realize something was wrong or that this was a problem until I kept getting clogs. This was caused by the heater being too far away from the nozzle. I would suggest putting the nozzle in first so you can get it to the right position (slightly below, <a href="https://ueeshop.ly200-cdn.com/u_file/UPAT/UPAT086/2205/04/products/4-e8fa.jpg" target="_blank">but not actually touching</a>, the ceramic heater), then the heatbreak and heatsink. Once you put the orange silicone sock on, <a href="https://ueeshop.ly200-cdn.com/u_file/UPAT/UPAT086/2205/04/products/5-6820.jpg">the sock should be wrapped around the hex-shape of the nozzle with just the cone shaped tip coming out</a>. If have a lot more sticking out then your nozzle is probably too low. It should go without saying but you need to make sure the heat break is screwed in enough to touch the nozzle. 
  - Don't expect this to be the last time you build the toolhead. It will need taken apart to change nozzles, to deal with clogs, to replace your ptfe tube, etc, etc. I think I probably took mine apart at least 10-15 times during the tuning phase. It's annoying at first, but you get faster at it and then it starts to feel like a Formula 1 pit stop. 

## Fastener locations
The viewer below allows you to view the different parts and has them highlighted with different colors to indicate where various fasteners go.

Use the dropdown above the viewer to change between models.

<div class="row bd">
  🟢 indicates a screw (only highlighted where the screw head is visible)<br>
  🔵 indicates a nut<br>
  🔴 indicates a heat insert<br>
</div>
<br>

<!-- Import maps polyfill -->
<!-- Remove this when import maps will be widely supported -->
<script async src="https://unpkg.com/es-module-shims@1.6.3/dist/es-module-shims.js"></script>
<script type="importmap">
  {
    "imports": {
      "three": "https://unpkg.com/three@v0.155.0/build/three.module.js",
      "three/addons/": "https://unpkg.com/three@v0.155.0/examples/jsm/"
    }
  }
</script>

<script>
  const params = {
    asset: 'chc_pro_mount',
    STL: 'chc_pro_mount'
  };

    const assets = [
    'chc_pro_mount',
    'chc_pro_clamp',
    'chc_pro_fanduct',
    'rod_cradle'
  ];
</script>

<script type="module" src="/js/viewer.js"></script>

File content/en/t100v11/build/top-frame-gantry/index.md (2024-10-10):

---
title: "Top frame & gantry build"
ogTitle: "Top Frame and Gantry Build - THE 100 Build Guide"
description: "How to build THE 100's v1.1 top frame & gantry"
lead: ""
date: 2023-08-14T14:41:39+01:00
draft: false
images: []
type: docs
menu:
  t100v11:
    parent: "build-v11"
weight: 515
toc: true
doc: t100v11
images: 
  - images/tfd_top_frame_preview.png
---
# Top Frame and Gantry Build

The top frame holds the toolhead, A/B (aka X/Y) motors, extruder, and extruder motor. Getting this part right is critical for the rest of the printer. It's also fun because you will finally get a sense of how the printer will look.

Visit the <a href="/t100/1.1/printing-guide/top-frame/">print & purchase guide for the top frame</a> and for <a href="/t100/1.1/printing-guide/gantry/">the gantry</a> to see what parts you will need to complete this part of the build. 

Then you should watch <a href="https://www.youtube.com/watch?v=g_kgOLjIEg0" target="_blank">Matt's video</a> for building the top frame. This guide will simply function as a supplement to that video. 

## Notes on the video
  - Matt doesn't really cover what screws he uses in the top frame (they're mostly m3x12 btw). All necessary screws are noted in the <a href="/t100/1.1/printing-guide/top-frame/">print & purchase guide for the top frame</a>.
  - While giving a brief overview of where heat inserts go (<a href="https://youtu.be/g_kgOLjIEg0?t=114" target="_blank">1:54</a>), he skips over talking about a few spots. They're shown in the beginning montage but I wanted to mention the ones he doesn't point out:
    - Heat inserts on the back and side where the back frame pieces will attach
    - Heat inserts for the extruder mount
    - Heat inserts for the gantry carriages
  - There is an m3 nut that needs inserted in the belt fasteners BEFORE you insert the bearings (<a href="https://youtu.be/g_kgOLjIEg0?t=323" target="_blank">5:23</a>) because you can't fit it in after. If you don't get a tight fit on the nut then you may want to glue it in so it doesn't fall out before needed. 

## Tips
  - His tip in the video to use a screw to remove the rods if needed is a life saver (<a href="https://youtu.be/g_kgOLjIEg0?t=237" target="_blank">3:57</a>).
  - When you insert the m5 screw in the belt fastener (<a href="https://youtu.be/g_kgOLjIEg0?t=323" target="_blank">5:23</a>) you don't want the bottom of the screw sticking out of the bottom of the printed part. Just screw it in until the bottom of the screw is flush with the bottom of the part. You will have trouble inserting it in the frame later if it sticks out; there is plenty of extra room at the top where the bolt head is. 
  - Repeating what I said about the toolhead build: There are various qualities of drylins, and how they work with your linear rods will vary. I bought some that were so tight I could barely move them, and others that were super smooth but a bit loose. In the end I actually switched from drylins to linear bearings as I didn't mind the sound difference and they just worked better for me. 
  - It can be an extremely tight fit to get the x-axis linear rods inserted in to the gantry pieces (<a href="https://youtu.be/g_kgOLjIEg0?t=417" target="_blank">6:57</a> and <a href="https://youtu.be/g_kgOLjIEg0?t=445" target="_blank">9:06</a>). You really need to apply some force to get them inserted all the way. If you don't get them in far enough then you won't be able to get the gantry properly installed. On one of mine I actually used my soldering iron to heat up the end of the rod slightly so it would go in easier (do so at your own risk). If the rods that run in the y-axis (front to back) don't fully seat where they're supposed to go then you likely haven't gotten the x-axis rods fully inserted. It may be easier to take it out of the frame and get both sides really pushed in, then remove the rods from the gantry pieces (see the first tip at the top of this list!) and try installing in the frame again.
  - I mentioned in the toolhead build section that it won't be your last time building the toolhead. This also won't be your last time assembling the gantry as you often have to take the linear rods off to get the toolhead off for maintenance. Don't worry, it gets easier every time you do it. 

## Fastener locations
The viewer below allows you to view the different parts and has them highlighted with different colors to indicate where various fasteners go.

Use the dropdown above the viewer to change between models.

<div class="row bd">
  🟢 indicates a screw (only highlighted where the screw head is visible)<br>
  🔵 indicates a nut<br>
  🔴 indicates a heat insert<br>
</div>
<br>

<!-- Import maps polyfill -->
<!-- Remove this when import maps will be widely supported -->
<script async src="https://unpkg.com/es-module-shims@1.6.3/dist/es-module-shims.js"></script>
<script type="importmap">
  {
    "imports": {
      "three": "https://unpkg.com/three@v0.155.0/build/three.module.js",
      "three/addons/": "https://unpkg.com/three@v0.155.0/examples/jsm/"
    }
  }
</script>

<script>
  const params = {
    asset: 'belt_fastener',
    STL: 'belt_fastener'
  };

    const assets = [
    'belt_fastener',
    'rod_holder',
    'connector_z',
    'back_left',
    'back_right',
    'front_left',
    'front_right',
    'connector_back_1',
    'connector_back_2',
    'connector_top_1',
    'connector_top_2',
    'connector_side_1',
    'connector_side_2'
  ];
</script>

<script type="module" src="/js/viewer.js"></script>

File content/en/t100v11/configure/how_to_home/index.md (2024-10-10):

---
title: "How to home"
ogTitle: "Homing your printer for the first time - THE 100 Build Guide"
description: "How to setup the sensorless homing macro, and then home for the first time!"
lead: ""
date: 2023-10-02T14:41:39+01:00
draft: false
images: []
type: docs
menu:
  t100v11:
    parent: "configure-v11"
weight: 680
toc: true
doc: t100v11
images: 
  - images/tfd_preview_home.png
---

# There's no place like home
The guide for homing your printer could have been much shorter, but I'm hoping people use these guides to learn just as much as they do to accomplish something. I also could have made the guides 100x longer and gone in to much more detail, but I want people to actually read them instead of saying "this is way too much!" 

We're finally close... let's slide in to home.

## Requirements 
  * You have completed the <a href="/t100/1.1/configure/sensorless-homing-prep/">sensorless homing prep</a> guide and your `printer.cfg` matches how we ended the bed movement guide.
  * Know how to do an emergency stop in fluidd/mainsail so you can immediately stop the homing process if your stepper driver if needed. This will help prevent damage to the printer and motion systems. 
      * 

<div class="alert alert-warning" role="alert">
    🛑	Skipping steps and not slowly iterating will result in you getting increasingly frustrated. It's important to make one change at a time, test one thing at a time, and document your progress as you go. If you've made it this far then you're doing great! But for those that have never setup a printer like this before, this is where a lot of frustration will come if you aren't patient and methodical about your setup.
</div>

<div class="alert alert-danger" role="alert">
    🛑	CORRECTION: Prior to 2023-10-03 I had "max_accel: 300", but it was causing homing issues. Please update your printer.cfg to "max_accel: 1000" to prevent issues with the following steps.
</div>

## Homing macro
The standard homing gcode command is `G28`. The issue with using the default command is the way THE 100 needs to home is different from the norm. This is because we use sensorless homing on all 3 axis, and because we use part of the homing process to ensure the dual Z motors are equal so that the bed is level. 

To override the default `G28` behavior, we have to add a few custom macros to our `printer.cfg`. I'm going to just include the macros and steps to install first, and later I'll explain how they work.

### Add the macro
Open your `printer.cfg` and scroll to the bottom. Paste the following below the last line

```
##### HOMING MACROS START #####

[gcode_macro G28]
rename_existing: G280
gcode:
  M80
  SET_KINEMATIC_POSITION Z=0
  G90
  G1 Z5 F200
  SENSORLESS_HOME_X
  SENSORLESS_HOME_Y
  SENSORLESS_HOME_Z

[gcode_macro SENSORLESS_HOME_X]
gcode:
    SENSORLESS_DELAY
    # Home
    G280 X
    # Move away
    G1 X{ printer.toolhead.axis_maximum.x/2 } F6000

[gcode_macro SENSORLESS_HOME_Y]
gcode:
    SENSORLESS_DELAY
    # Home
    G280 Y
    # Move away
    G90
    G1 Y{ printer.toolhead.axis_maximum.y/2 } F6000

[gcode_macro SENSORLESS_HOME_Z]
gcode:
    SENSORLESS_DELAY
    # Home
    G1 X{ printer.toolhead.axis_maximum.x/2 } Y{ printer.toolhead.axis_maximum.y } F6000
    G280 Z
    SET_KINEMATIC_POSITION Z=1
    G1 Z0 F120
    G1 Z5 F120
    SENSORLESS_DELAY
    G280 Z
    G1 Z5 F120   # Make sure we clear the toolhead
    G1 X{ printer.toolhead.axis_minimum.x +5 } Y{ printer.toolhead.axis_maximum.y -2 } F6000

[gcode_macro SENSORLESS_DELAY]
gcode:
    # Pause to ensure driver stall flag is clear
    G4 P2000

[gcode_macro M80]
gcode:
  SET_STEPPER_ENABLE STEPPER=stepper_x ENABLE=1
  SET_STEPPER_ENABLE STEPPER=stepper_y ENABLE=1
  SET_STEPPER_ENABLE STEPPER=stepper_z ENABLE=1

##### HOMING MACROS END #####
```

Then click `Save & Restart`.

## Your first home
The time as finally come to home for the first time! I would highly suggest two things before continuing:
  1. Restart Klipper to have a clean slate: 3 dots in the top right > Service > Klipper > Restart icon
  1. Manually move your printhead to roughly the middle of the gantry and slightly lower the bed just to give things the best chance of working right

Press the `🏠 All` button in fluidd, or send `G28` via the console. Be prepared to hit `Emergency Stop` if needed!

If all goes well then your printer should follow these steps:

  1. Bed moves down slightly
  1. Toolhead moves to the right until it contacts the frame. It then moves to the center of the bed. 
  1. Toolhead moves to the back until it contacts the frame. It then moves to the center of the bed. 
  1. Toolhead moves to the back of the frame again -- this is done to avoid the bed colliding with it
      1. Note: If you're using a modified bed that isn't the original, you may have issues with the bed colliding due to the size. The proper fix for that is to use an actual endstop on the Z-axis.
  1. Bed moves down slightly, then up until it contacts the frame
  1. Bed moves down slightly again, then up until it contacts the frame again
  1. Bed moves down, then toolhead moves to the back left

Your printer is now homed!!

### Troubleshooting
  * If your toolhead homes to the left instead of right, or front instead of back
      * If you completed all the steps required to ensure your motors move in the proper direction then this probably isn't an issue. The direction it homes is controlled by the `position_endstop` settings in your printer.cfg and they ultimately don't actually matter. If you followed my guide then they SHOULD be going to the right and to the back, but <b><u>as long as position `0,0` is in the front left corner of the bed then it doesn't actually matter</b></u>. 
  * If you encounter some other issue, please post about it in Discord

<div class="alert alert-info" role="alert">
    💾 	Take a moment now to download a copy of your `printer.cfg` to your computer and rename it to include today's date, or `printer.cfg-homing_works` or something like that. If you end up breaking your cfg in future steps, or if your SD card gets corrupted, or anything else like that... you'll be glad you have this saved! I highly recommend repeating this process any time you make important cfg changes. 
</div>

Now that your printer is homing correctly, let's get the other components working. Or continue reading if you're interested in what the macro does. 

## The macro explained
Coming soon. Focusing on moving the guide forward for now. Ping me in discord if this is important to you and I'll work on it.

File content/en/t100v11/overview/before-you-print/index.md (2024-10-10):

---
title: "Before you print"
ogTitle: "Before you print - THE 100 Print Guide" 
description: "What to know before you start printing THE 100 3d printer"
lead: ""
date: 2023-06-18T14:41:39+01:00
lastmod: 2023-06-21T00:41:39+01:00
draft: false
images: []
type: docs
menu:
  t100v11:
    parent: "overview-v11"
    identifier: "before-you-print-v11"
weight: 70
toc: true
doc: t100v11
static_images: true
images: 
  - tfd_the100_preview.png
---
# Before you start printing

The official BOM is available <a href="https://docs.google.com/spreadsheets/d/1qVG3n-1HVcA7c-vKpUakU7fWirMONmqOiJRv8SHPkTo/edit#gid=0">here</a>, and I have a detailed list here. I suggest reviewing them and confirming you can get everything you need prior to starting to print the parts. 

## STL Links
The files for v1.1 have only been made available in beta to Matt's <a href="https://www.patreon.com/The100">Patreon</a> supporters so I can't provide links to the downloads. I will get links added once it is made available to the public.

## Warning
Version 1.1 is a major work-in-progress. There are going to be broken images, broken links, and missing info while I work on it. But I'm publishing my progress as I go so it can still be of some use. The current revision of this guide is based on THE 100 v1.1-beta1. That means my counts for screws and heat inserts may be slightly off once v1.1-final is released. It should be very close though.

I will be updating this guide to reference v1.1-final once it is released.

## Print details
This guide includes details such as how much filament is used to print a part. Note that these numbers are always for a quantity of 1. If a particular part requires 4 then you need to multiply the filament length/weight by 4. The same is true for assembly hardware counts.

ℹ️ Weights are for PLA based on a density of 1.24 g/cm<sup>3</sup>.

### Print time
Using a standard stock Ender 3 style printer at typical speeds and based on the print settings below, you should expect the whole printer to take about 173 hours to print. It can absolutely be much less than that if you're using a faster or upgraded printer, but the typical maker should expect around that number.

ℹ️ The estimated print times displayed in the print guide are based on a stock Ender 3 using default settings.

## Print settings
The <a href="https://github.com/MSzturc/the100#print-settings">recommended print settings</a> are:

  * 0.4 or 0.6 nozzle (0.6 will be slightly faster, but you can use either)
  * 0.25 Layer height
  * 0.5 Line width
  * 3 Top layers
  * 3 Bottom layers
  * 3 Walls
  * Grid Infill Pattern
  * 25% Infill
    * Use 30% infill for the print bed to move the center of gravity to where it's needed

## Assembly hardware
Each section includes details on the parts you need to purchase for assembly. I decided the easiest way to assign where to list a screw or a heat insert is:
  * Heat inserts are assigned to the object where they actually get put in to
  * Screws are assigned to the object where you see the screw head

As mentioned above under <a href="#print-details">print details</a>, the quantity of heat inserts and screws at a per-part level is based on a quantity of 1. If you need 4 of a particular part, multiply the heat insert/screw count by 4.  

## Additional info and support

This project wouldn't exist without Matt so I wanted to provide a list of links back to him and his resources:

  * <a href="https://github.com/MSzturc/the100">GitHub</a>
  * <a href="https://discord.gg/fW7BcUErgZ">Discord</a>
    * You can find me on here as `TheForgetfulDev`. Please reach out if you notice any issues with this guide or if you have any questions about the build.
  * <a href="https://www.patreon.com/The100">Patreon</a>
  * <a href="https://www.youtube.com/playlist?list=PLM01o_dfwbDcKYB-9yV0vLs5k0CrHUv0W">YouTube</a>
  * <a href="https://hackaday.io/project/190348-the-100-the-fastest-3d-printer">hackaday</a>

Ready to get the process started? <a href="/t100/1.1/overview/bill-of-materials/">Check out the BOM</a> to see what parts you can't print.

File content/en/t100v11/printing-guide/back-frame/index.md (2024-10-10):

---
title: "Back Frame"
ogTitle: "Back Frame - THE 100 Print Guide"
description: "How to print THE 100's v1.1 back frame, as well as what hardware you need to purchase to build it."
lead: ""
date: 2023-06-22T14:41:39+01:00
draft: false
images: []
type: docs
menu:
  t100v11:
    parent: "printing-guide-the100"
weight: 400
toc: true
doc: t100v11
images: 
  - images/tfd_back_frame_preview.png
---
# Back Frame
The back frame is one of the big changes from v1.0 to v1.1. It removes 2 rods from the back and solidifies the whole frame. 

<div class="row bd">
  <div class="col">
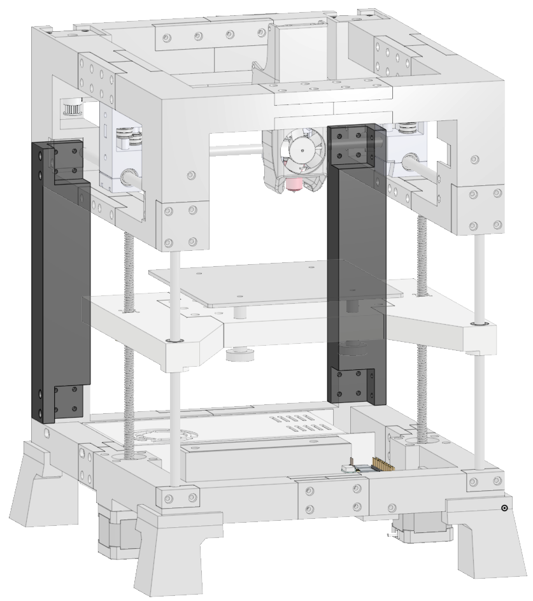
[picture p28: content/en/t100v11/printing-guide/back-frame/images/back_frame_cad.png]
      

  </div>
  <div class="col">
    <ul class="list-group">
      <li class="list-group-item d-flex justify-content-between align-items-center">
        <div class="text fw-bold">Printed parts</div>
        <div class="text">2</div>
      </li>
    </ul>
    <br>
    <ul class="list-group">
      <li class="list-group-item d-flex justify-content-between align-items-center">
        <div class="text fw-bold">Purchased parts</div>
        <div class="text">24</div>
      </li>
    </ul>   
    <br>
    <ul class="list-group">
      <li class="list-group-item d-flex justify-content-between align-items-center">
        <div class="text fw-bold">Filament</div>
        <div class="text">80m | 238.6g</div>
      </li>
    </ul>   
    <br>
    <ul class="list-group">
      <li class="list-group-item d-flex justify-content-between align-items-center">
        <div class="text fw-bold">Print time</div>
        <div class="text">10h 56m</div>
      </li>
    </ul>  
  </div>
</div>

### Printed parts

<table class="table table-sm">
  <thead>
    <tr>
      <th scope="col">Part Name</th>
      <th scope="col">STL</th>
      <th scope="col">Qty</th>
      <th scope="col">Notes</th>
    </tr>
  </thead>
  <tbody>
    <tr>
      <td>Back Connector Left</td>
      <td class="no-wrap"><a target="_blank" href="https://github.com/MSzturc/t100/blob/main/STL/Back/Back%20Connector%20Left.stl">github</a> / <a href="https://files.printables.com/media/prints/572689/stls/4585086_c556e237-101a-4acd-a392-098b7c88e9a1/back-connector-left.stl">printables</a></td>
      <td>1</td>
      <td><a href="#back-frame-1">More info</a></td>
    </tr>
    <tr>
      <td>Back Connector Right</td>
      <td class="no-wrap"><a target="_blank" href="https://github.com/MSzturc/t100/blob/main/STL/Back/Back%20Connector%20Right.stl">github</a> / <a href="https://files.printables.com/media/prints/572689/stls/4585087_9b00f09c-1c11-4350-a192-ece4abe3a657/back-connector-right.stl">printables</a></td>
      <td>1</td>
      <td><a href="#back-frame-1">More info</a></td>
    </tr>
  </tbody>
</table>

### Purchased Parts
<table class="table table-sm no-margin">
  <thead>
    <tr>
      <th scope="col">Item</th>
      <th scope="col">Qty</th>
      <th scope="col">Notes</th>
    </tr>
  </thead>
  <tbody>
    <tr>
      <td>m3x10 screw</td>
      <td>24</td>
      <td></td>
    </tr>
  </tbody>
</table>

### Details
#### Back frame
  
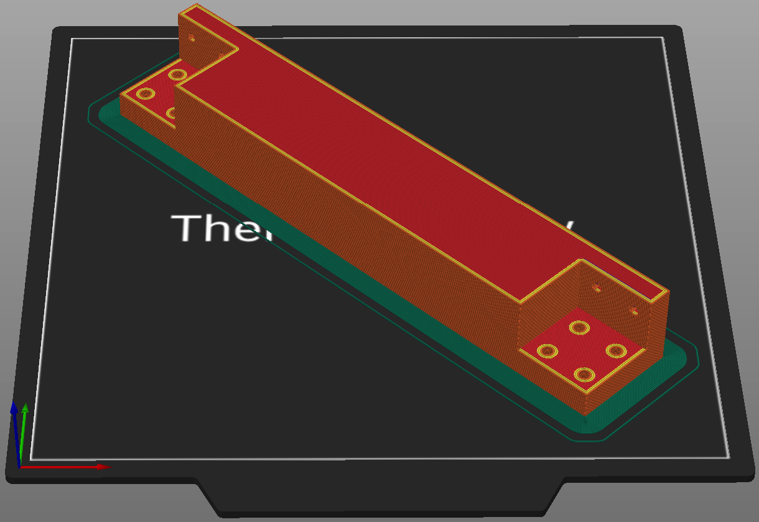
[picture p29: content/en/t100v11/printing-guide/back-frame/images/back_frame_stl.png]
  
##### Print
<table class="table table-striped table-hover no-margin">
  <tbody class="table-group-divider">
    <tr>
      <th scope="row" class="no-wrap">Quantity</th>
      <td> </td>
      <td>2</td>
    </tr>
    <tr>
      <th scope="row" class="no-wrap">Print Time</th>
      <td> </td>
      <td>36m</td>
    </tr>
    <tr>
      <th scope="row" class="no-wrap">Filament Length</th>
      <td> </td>
      <td>40m</td>
    </tr>
    <tr>
      <th scope="row" class="no-wrap">Filament Weight</th>
      <td> </td>
      <td>119.3g</td>
    </tr>
    <tr>
      <th scope="row" class="no-wrap">Supports?</th>
      <td> </td>
      <td>Yes - only in the countersunk holes touching the build plate.</td>
    </tr>
    <tr>
      <th scope="row">Note</th>
      <td> </td>
      <td>There are 2 different STLs but in reality it's the same part twice.</td>
    </tr>
  </tbody>
</table>

##### Purchase
<table class="table table-striped table-hover no-margin">
  <thead>
    <tr>
      <th scope="col">Item</th>
      <th scope="col">Qty</th>
      <th scope="col">Note</th>
    </tr>
  </thead>
  <tbody>
    <tr>
      <td>m3x10 screw</td>
      <td>12</td>
      <td></td>
    </tr>
  </tbody>
</table>

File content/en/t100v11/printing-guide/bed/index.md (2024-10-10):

---
title: "Bed"
ogTitle: "Bed - THE 100 Print Guide"
description: "How to print THE 100's v1.1 bed, as well as what hardware you need to purchase to build it."
lead: ""
date: 2023-06-18T14:41:39+01:00
draft: false
images: []
type: docs
menu:
  t100v11:
    parent: "printing-guide-the100"
weight: 350
toc: true
doc: t100v11
images: 
  - images/tfd_bed_preview.png
---
# Bed
As mentioned in <a href="/t100/1.1/overview/before-you-print/#print-settings">print settings</a>, these parts should be printed with 30% infill. 

<div class="row bd">
  <div class="col">
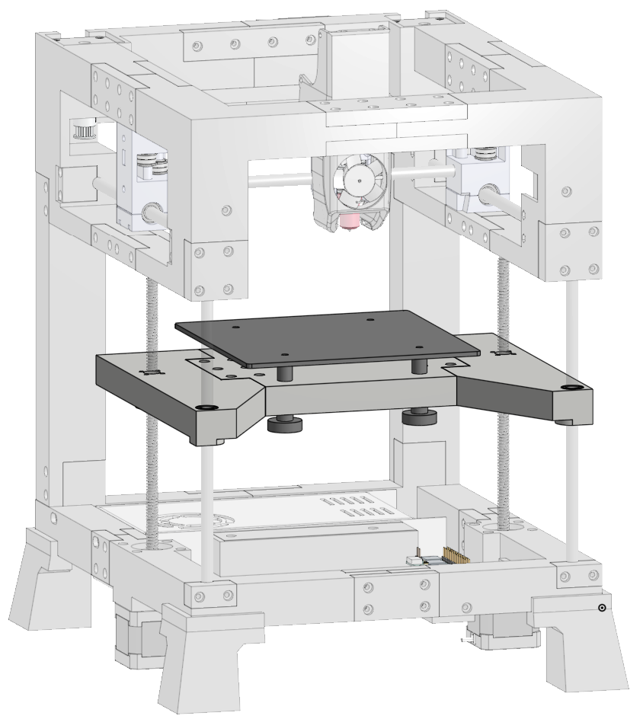
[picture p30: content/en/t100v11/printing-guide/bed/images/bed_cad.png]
      
  </div>
  <div class="col">
    <ul class="list-group">
      <li class="list-group-item d-flex justify-content-between align-items-center">
        <div class="text fw-bold">Printed parts</div>
        <div class="text">3</div>
      </li>
    </ul>
    <br>
    <ul class="list-group">
      <li class="list-group-item d-flex justify-content-between align-items-center">
        <div class="text fw-bold">Purchased parts</div>
        <div class="text">35</div>
      </li>
    </ul>   
    <br>
    <ul class="list-group">
      <li class="list-group-item d-flex justify-content-between align-items-center">
        <div class="text fw-bold">Filament</div>
        <div class="text">156m | 465g</div>
      </li>
    </ul>   
    <br>
    <ul class="list-group">
      <li class="list-group-item d-flex justify-content-between align-items-center">
        <div class="text fw-bold">Print time</div>
        <div class="text">21h 0m</div>
      </li>
    </ul>   
  </div>
</div>

### Printed parts
<table class="table table-sm">
  <thead>
    <tr>
      <th scope="col">Part Name</th>
      <th scope="col">STL</th>
      <th scope="col">Qty</th>
      <th scope="col">Notes</th>
    </tr>
  </thead>
  <tbody>
    <tr>
      <td>Center</td>
      <td class="no-wrap"><a target="_blank" href="https://github.com/MSzturc/t100/blob/main/STL/Bed/Center.stl">github</a> / <a href="https://files.printables.com/media/prints/572689/stls/4581588_09eb6d6c-8caa-4684-978e-19dcb8971a19/center.stl">printables</a></td>
      <td>1</td>
      <td><a href="#center">More info</a></td>
    </tr>
    <tr>
      <td>Left</td>
      <td class="no-wrap"><a target="_blank" href="https://github.com/MSzturc/t100/blob/main/STL/Bed/Left.stl">github</a> / <a href="https://files.printables.com/media/prints/572689/stls/4581590_128c4603-3ed4-423d-9a37-d211a697060c/left.stl">printables</a></td>
      <td>1</td>
      <td><a href="#left">More info</a></td>
    </tr>
    <tr>
      <td>Right</td>
      <td class="no-wrap"><a target="_blank" href="https://github.com/MSzturc/t100/blob/main/STL/Bed/Right.stl">github</a> / <a href="https://files.printables.com/media/prints/572689/stls/4581589_b78f9bc8-574d-4154-bc54-77deda70e43d/right.stl">printables</a></td>
      <td>1</td>
      <td><a href="#right">More info</a></td>
    </tr>
  </tbody>
</table>

### Purchased Parts
<table class="table table-sm no-margin">
  <thead>
    <tr>
      <th scope="col" width="30%">Item</th>
      <th scope="col" width="10%">Qty</th>
      <th scope="col" width="60%">Notes</th>
    </tr>
  </thead>
  <tbody>
    <tr>
      <td>m3x10 screw</td>
      <td>8</td>
      <td></td>
    </tr>
    <tr>
      <td>m3x20 screw</td>
      <td>12</td>
      <td></td>
    </tr>
    <tr>
      <td>m3 nut</td>
      <td>12</td>
      <td></td>
    </tr>
    <tr>
      <td class="no-wrap">LM8UU steel bearing</td>
      <td>2</td>
      <td></td>
    </tr>
    <tr>
      <td>Bed spring kit</td>
      <td>1</td>
      <td>More than a singular item but is sold as a kit. 4 springs, 4 adjustment nuts. 4 screws. The kit I got was m4x40.</td>
    </tr>
  </tbody>
</table>

### Details

#### Center
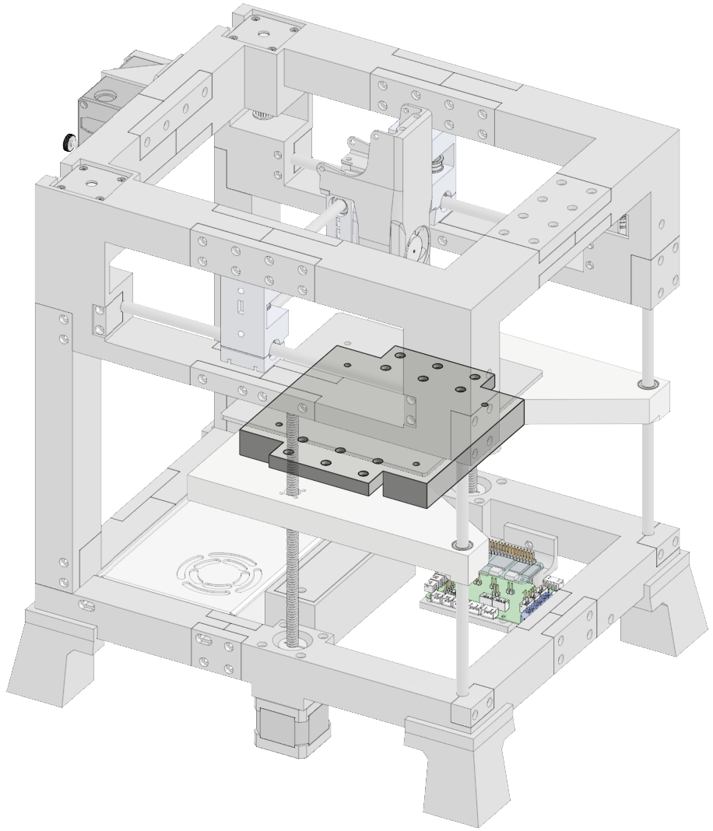
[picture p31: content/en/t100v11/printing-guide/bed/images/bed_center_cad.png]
  
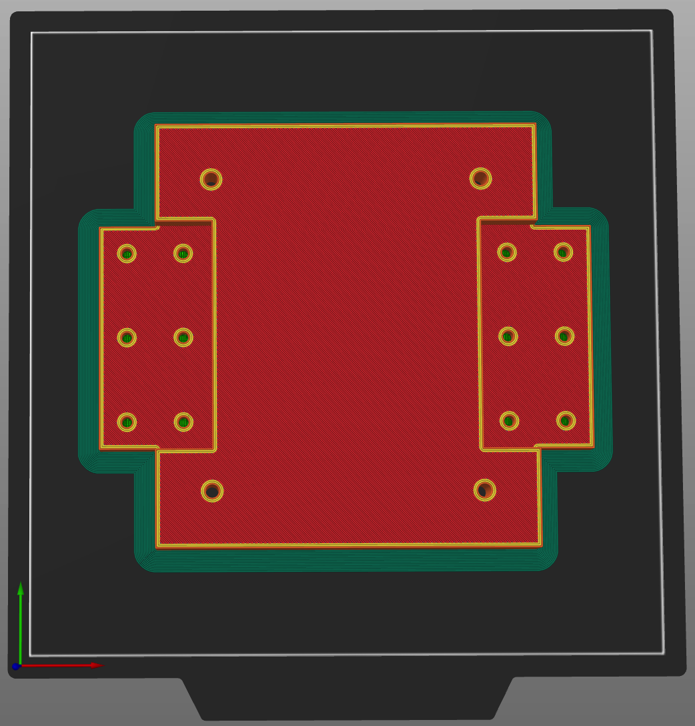
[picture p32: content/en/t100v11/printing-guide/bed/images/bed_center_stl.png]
  
##### Print
<table class="table table-striped table-hover no-margin">
  <tbody class="table-group-divider">
    <tr>
      <th scope="row" class="no-wrap">Quantity</th>
      <td> </td>
      <td>1</td>
    </tr>
    <tr>
      <th scope="row" class="no-wrap">Filament Length</th>
      <td> </td>
      <td>72m</td>
    </tr>
    <tr>
      <th scope="row" class="no-wrap">Filament Weight</th>
      <td> </td>
      <td>215g</td>
    </tr>
    <tr>
      <th scope="row" class="no-wrap">Supports?</th>
      <td> </td>
      <td>No</td>
    </tr>
    <tr>
      <th scope="row" class="no-wrap">Note</th>
      <td> </td>
      <td>A brim is recommended to help keep the bed from warping. </td>
    </tr>
  </tbody>
</table>

##### Purchase
<table class="table table-striped table-hover no-margin">
  <thead>
    <tr>
      <th scope="col">Item</th>
      <th scope="col">Qty</th>
      <th scope="col">Note</th>
    </tr>
  </thead>
  <tbody>
    <tr>
      <td>m3 nut</td>
      <td>12</td>
      <td></td>
    </tr>
  </tbody>
</table>

#### Left
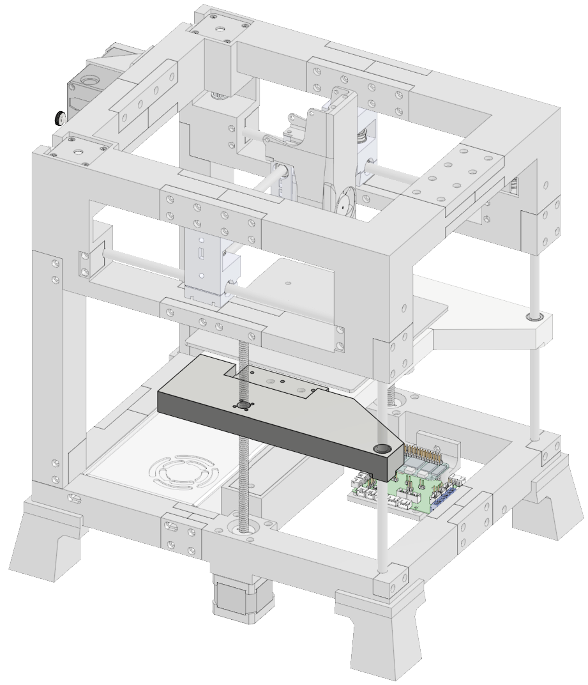
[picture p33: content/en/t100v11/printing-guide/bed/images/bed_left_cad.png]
  
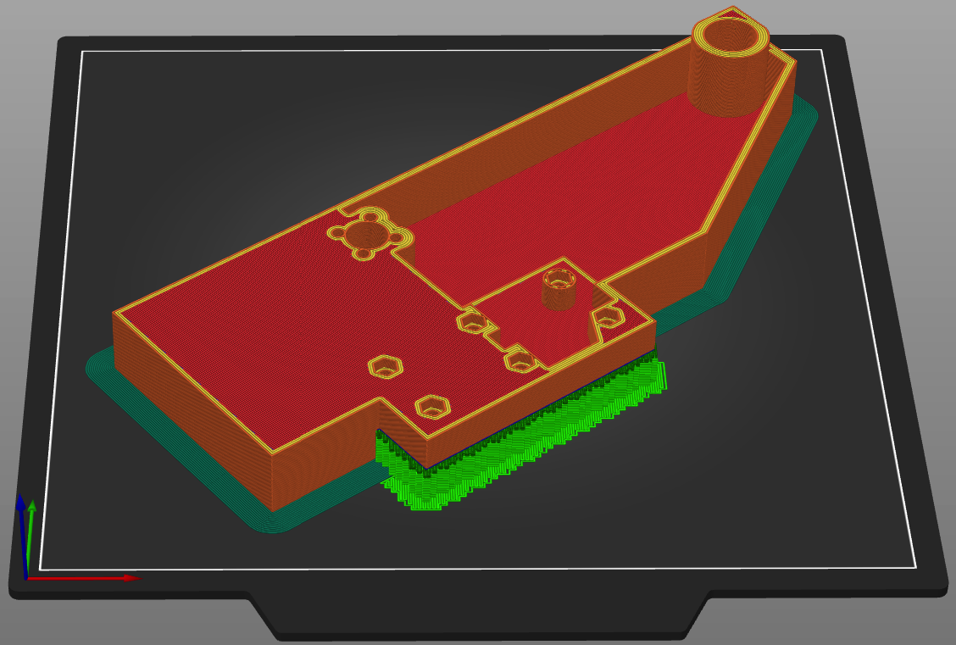
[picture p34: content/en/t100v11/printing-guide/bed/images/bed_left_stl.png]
  
##### Print
<table class="table table-striped table-hover no-margin">
  <tbody class="table-group-divider">
    <tr>
      <th scope="row" class="no-wrap">Quantity</th>
      <td> </td>
      <td>1</td>
    </tr>
    <tr>
      <th scope="row" class="no-wrap">Filament Length</th>
      <td> </td>
      <td>42m</td>
    </tr>
    <tr>
      <th scope="row" class="no-wrap">Filament Weight</th>
      <td> </td>
      <td>125g</td>
    </tr>
    <tr>
      <th scope="row" class="no-wrap">Supports?</th>
      <td> </td>
      <td>Yes</td>
    </tr>
    <tr>
      <th scope="row" class="no-wrap">Note</th>
      <td> </td>
      <td>A brim is recommended to help keep the bed from warping. Needs to be oriented at an angle to fit on a 225x225 bed like the Ender 3 (or be willing to override settings in your slicer to tell it to slice anyways).</td>
    </tr>
  </tbody>
</table>

##### Purchase
<table class="table table-striped table-hover no-margin">
  <thead>
    <tr>
      <th scope="col">Item</th>
      <th scope="col">Qty</th>
      <th scope="col">Note</th>
    </tr>
  </thead>
  <tbody>
    <tr>
      <td>m3x10</td>
      <td>4</td>
      <td>For the lead screw nut</td>
    </tr>
    <tr>
      <td>m3x20 screw</td>
      <td>6</td>
      <td></td>
    </tr>
  </tbody>
</table>

#### Right
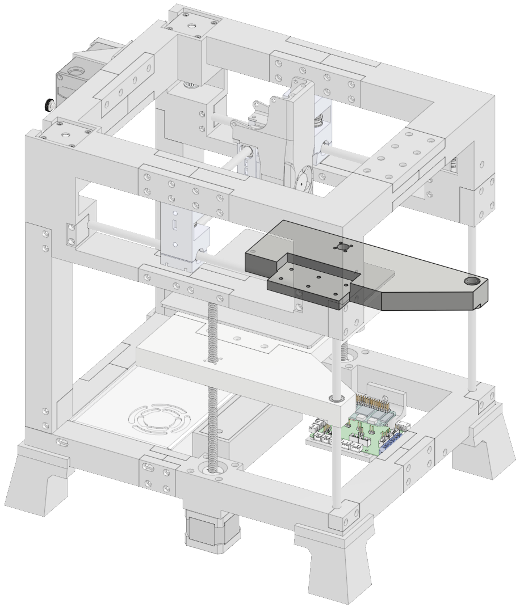
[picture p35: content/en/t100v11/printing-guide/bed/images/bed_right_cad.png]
  
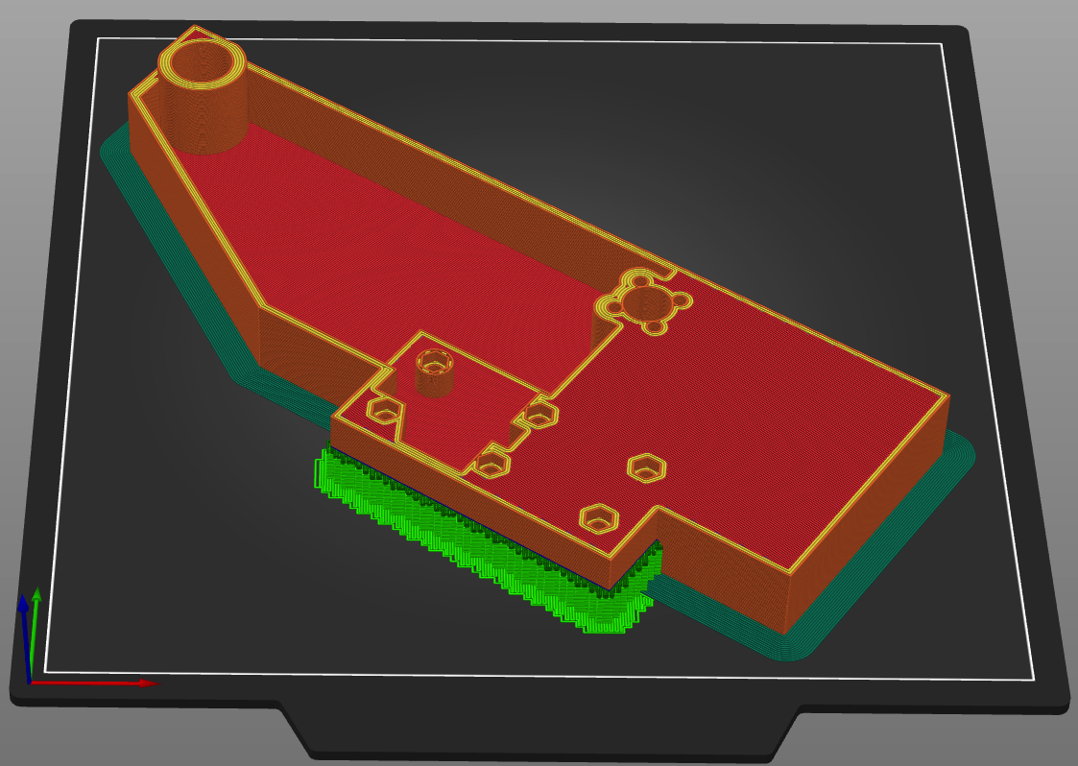
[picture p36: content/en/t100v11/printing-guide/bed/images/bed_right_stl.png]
  
##### Print
<table class="table table-striped table-hover no-margin">
  <tbody class="table-group-divider">
    <tr>
      <th scope="row" class="no-wrap">Quantity</th>
      <td> </td>
      <td>1</td>
    </tr>
    <tr>
      <th scope="row" class="no-wrap">Filament Length</th>
      <td> </td>
      <td>42m</td>
    </tr>
    <tr>
      <th scope="row" class="no-wrap">Filament Weight</th>
      <td> </td>
      <td>125g</td>
    </tr>
    <tr>
      <th scope="row" class="no-wrap">Supports?</th>
      <td> </td>
      <td>Yes</td>
    </tr>
    <tr>
      <th scope="row" class="no-wrap">Note</th>
      <td> </td>
      <td>A brim is recommended to help keep the bed from warping. Needs to be oriented at an angle to fit on a 225x225 bed like the Ender 3 (or be willing to override settings in your slicer to tell it to slice anyways).</td>
    </tr>
  </tbody>
</table>

##### Purchase
<table class="table table-striped table-hover no-margin">
  <thead>
    <tr>
      <th scope="col">Item</th>
      <th scope="col">Qty</th>
      <th scope="col">Note</th>
    </tr>
  </thead>
  <tbody>
    <tr>
      <td>m3x10</td>
      <td>4</td>
      <td>For the lead screw nut</td>
    </tr>
    <tr>
      <td>m3x20 screw</td>
      <td>6</td>
      <td></td>
    </tr>
  </tbody>
</table>

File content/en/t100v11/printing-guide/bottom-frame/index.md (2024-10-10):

---
title: "Bottom Frame"
ogTitle: "Bottom Frame - THE 100 Print Guide"
description: "How to print THE 100's v1.1 bottom frame, as well as what hardware you need to purchase to build it."
lead: ""
date: 2023-06-18T14:41:39+01:00
draft: false
images: []
type: docs
menu:
  t100v11:
    parent: "printing-guide-the100"
weight: 340
toc: true
doc: t100v11
images: 
  - images/tfd_bottom_frame_preview.png
---
# Bottom Frame

<div class="row bd">
  <div class="col">
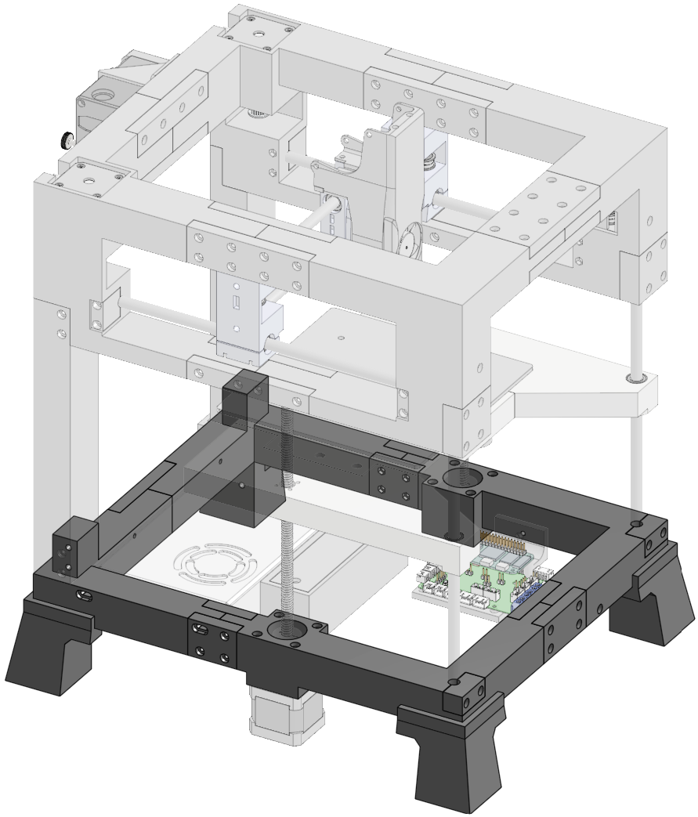
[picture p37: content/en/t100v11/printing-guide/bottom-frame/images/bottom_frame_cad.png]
      
  </div>
  <div class="col">
    <ul class="list-group">
      <li class="list-group-item d-flex justify-content-between align-items-center">
        <div class="text fw-bold">Printed parts</div>
        <div class="text">19</div>
      </li>
    </ul>
    <br>
    <ul class="list-group">
      <li class="list-group-item d-flex justify-content-between align-items-center">
        <div class="text fw-bold">Purchased hardware</div>
        <div class="text">110</div>
      </li>
    </ul>   
    <br>
    <ul class="list-group">
      <li class="list-group-item d-flex justify-content-between align-items-center">
        <div class="text fw-bold">Filament</div>
        <div class="text">296.9m / 885.9g</div>
      </li>
    </ul>   
    <br>
    <ul class="list-group">
      <li class="list-group-item d-flex justify-content-between align-items-center">
        <div class="text fw-bold">Print time</div>
        <div class="text">44h 34m</div>
      </li>
    </ul>  
  </div>
</div>

### Printed Parts
<table class="table table-sm">
  <thead>
    <tr>
      <th scope="col">Part Name</th>
      <th scope="col">Link</th>
      <th scope="col">Qty</th>
      <th scope="col">Notes</th>
    </tr>
  </thead>
  <tbody>
    <tr>
      <td>Frame Back Left</a></td>
      <td class="no-wrap"><a target="_blank" href="https://github.com/MSzturc/t100/blob/main/STL/Bottom%20Frame/Frame%20Back%20Left.stl">github</a> / <a href="https://files.printables.com/media/prints/572689/stls/4581574_d26601dd-8dd4-467a-98df-87ee82356d1a/frame-back-left.stl">printables</a></td>
      <td>1</td>
      <td><a href="#frame-back-left">More info</a></td>
    </tr>
    <tr>
      <td>Frame Back Right</td>
      <td class="no-wrap"><a target="_blank" href="https://github.com/MSzturc/t100/blob/main/STL/Bottom%20Frame/Frame%20Back%20Right.stl">github</a> / <a href="https://files.printables.com/media/prints/572689/stls/4581583_f97f3d93-7a8d-412a-a32b-f8ce275d0b51/frame-back-right.stl">printables</a></td>
      <td>1</td>
      <td><a href="#frame-back-right">More info</a></td>
    </tr>
    <tr>
      <td>Frame Front Left</td>
      <td class="no-wrap"><a target="_blank" href="https://github.com/MSzturc/t100/blob/main/STL/Bottom%20Frame/Frame%20Front%20Left.stl">github</a> / <a href="https://files.printables.com/media/prints/572689/stls/4581571_fd5acb79-92c9-4185-875c-d3ac22fda0c7/frame-front-left.stl">printables</a></td>
      <td>1</td>
      <td><a href="#frame-front-left">More info</a></td>
    </tr>
    <tr>
      <td>Frame Front Right</td>
      <td class="no-wrap"><a target="_blank" href="https://github.com/MSzturc/t100/blob/main/STL/Bottom%20Frame/Frame%20Front%20Right.stl">github</a> / <a href="https://files.printables.com/media/prints/572689/stls/4581569_572aa844-b241-4efb-a8a3-06fefccff163/frame-front-right.stl">printables</a></td>
      <td>1</td>
      <td><a href="#frame-front-right">More info</a></td>
    </tr>
    <tr>
      <td>Frame Connector Back</td>
      <td class="no-wrap"><a target="_blank" href="https://github.com/MSzturc/t100/blob/main/STL/Bottom%20Frame/Frame%20Connector%20Back.stl">github</a> / <a href="https://files.printables.com/media/prints/572689/stls/4581584_1287f441-553b-4f64-b214-bc2e5e82d657/frame-connector-back.stl">printables</a></td>
      <td>1</td>
      <td><a href="#frame-connector-back">More info</a></td>
    </tr>
    <tr>
      <td>Frame Connector Front 2</td>
      <td class="no-wrap"><a target="_blank" href="https://github.com/MSzturc/t100/blob/main/STL/Bottom%20Frame/Frame%20Connector%20Front%202.stl">github</a> / <a href="https://files.printables.com/media/prints/572689/stls/4581585_24c4610e-94b8-4217-bb12-0506cf78156c/frame-connector-front-2.stl">printables</a></td>
      <td>1</td>
      <td><a href="#frame-connector-front-2">More info</a></td>
    </tr>
    <tr>
      <td>Frame Connector Front 1</td>
      <td class="no-wrap"><a target="_blank" href="https://github.com/MSzturc/t100/blob/main/STL/Bottom%20Frame/Frame%20Connector%20Front%201.stl">github</a> / <a href="https://files.printables.com/media/prints/572689/stls/4581580_50e3546e-36e2-4620-a702-d6faa6358e03/frame-connector-front-1.stl">printables</a></td>
      <td>1</td>
      <td><a href="#frame-connector-front-1">More info</a></td>
    </tr>
    <tr>
      <td>Frame Connector Left 1</td>
      <td class="no-wrap"><a target="_blank" href="https://github.com/MSzturc/t100/blob/main/STL/Bottom%20Frame/Frame%20Connector%20Left%201.stl">github</a> / <a href="https://files.printables.com/media/prints/572689/stls/4581575_2e6b2d10-429b-4f6b-b3b1-0845ad0ed513/frame-connector-left-1.stl">printables</a></td>
      <td>1</td>
      <td><a href="#frame-connector-left-1">More info</a></td>
    </tr>
    <tr>
      <td>Frame Connector Left 2</td>
      <td class="no-wrap"><a target="_blank" href="https://github.com/MSzturc/t100/blob/main/STL/Bottom%20Frame/Frame%20Connector%20Left%202.stl">github</a> / <a href="https://files.printables.com/media/prints/572689/stls/4581572_66d6eda2-33a6-4853-86ff-398617f07830/frame-connector-left-2.stl">printables</a></td>
      <td>1</td>
      <td><a href="#frame-connector-left-2">More info</a></td>
    </tr>
    <tr>
      <td>Frame Connector Right 1</td>
      <td class="no-wrap"><a target="_blank" href="https://github.com/MSzturc/t100/blob/main/STL/Bottom%20Frame/Frame%20Connector%20Right%201.stl">github</a> / <a href="https://files.printables.com/media/prints/572689/stls/4581577_ea51eae6-d738-48fd-869d-35d58253d572/frame-connector-right-1.stl">printables</a></td>
      <td>1</td>
      <td><a href="#frame-connector-right-1">More info</a></td>
    </tr>
    <tr>
      <td>Frame Connector Right 2</td>
      <td class="no-wrap"><a target="_blank" href="https://github.com/MSzturc/t100/blob/main/STL/Bottom%20Frame/Frame%20Connector%20Right%202.stl">github</a> / <a href="https://files.printables.com/media/prints/572689/stls/4581578_ac7c8794-6c97-4ba7-94ea-05155d08bf1a/frame-connector-right-2.stl">printables</a></td>
      <td>1</td>
      <td><a href="#frame-connector-right-2">More info</a></td>
    </tr>
    <tr>
      <td>Foot</td>
      <td class="no-wrap"><a target="_blank" href="https://github.com/MSzturc/t100/blob/main/STL/Bottom%20Frame/Foot%20Back%20Right.stl">github</a> / <a href="https://files.printables.com/media/prints/572689/stls/4581570_2f44b0b7-4560-49aa-a7bc-2151c762a710/foot-back-right.stl">printables</a></td>
      <td>4</td>
      <td><a href="#foot">More info</a></td>
    </tr>
    <tr>
      <td>5mm - 8mm Coupler</td>
      <td class="no-wrap"><a href="https://files.printables.com/media/prints/430339/stls/3564393_03d9394b-5c80-48cf-a571-ee4341b42e73/5mm-8mm-coupler.stl">printables</a></td>
      <td>2</td>
      <td><a href="#5mm---8mm-coupler">More info</a></td>
    </tr>
    <tr>
      <td>Connector Z-Rod</td>
      <td class="no-wrap"><a target="_blank" href="https://github.com/MSzturc/t100/blob/main/STL/Bottom%20Frame/Connector%20Z-Rod.stl">github</a> / <a href="https://files.printables.com/media/prints/572689/stls/4581582_e1111571-9778-4401-b52e-bfcbb22954a5/connector-z-rod.stl">printables</a></td>
      <td>2</td>
      <td><a href="#connector-z-rod">More info</a></td>
    </tr>
    <tr>
      <td>Power Cord Clamp</td>
      <td class="no-wrap"><a target="_blank" href="https://github.com/MSzturc/t100/blob/main/STL/Bottom%20Frame/Power%20Cord%20clamp.stl">github</a> / <a href="https://files.printables.com/media/prints/572689/stls/4581581_83c72922-f92e-48b9-b9c3-00fa7dcc0d5b/power-cord-clamp.stl">printables</a></td>
      <td>1</td>
      <td><a href="#power-cord-clamp">More info</a></td>
    </tr>
    <tr>
      <td>Cable Guide Clamp</td>
            <td class="no-wrap"><a target="_blank" href="https://github.com/MSzturc/t100/blob/main/STL/Bottom%20Frame/Cable%20Guide%20Clamp.stl">github</a> / <a href="https://files.printables.com/media/prints/572689/stls/4660166_9fbc03a8-48f0-4112-a0f6-4e9a807422e7/cable-guide-clamp.stl">printables</a></td>
      <td>2</td>
      <td><a href="#cable-guide-clamp">More info</a></td>
    </tr>
  </tbody>
</table>

### Purchased Parts
<table class="table table-sm no-margin">
  <thead>
    <tr>
      <th scope="col">Item</th>
      <th scope="col">Qty</th>
      <th scope="col">Notes</th>
    </tr>
  </thead>
  <tbody>
    <tr>
      <td>m3 heat insert</td>
      <td>42</td>
      <td></td>
    </tr>
    <tr>
      <td>m3 nut</td>
      <td>15</td>
      <td></td>
    </tr>
    <tr>
      <td>m3 washer</td>
      <td>8</td>
      <td></td>
    </tr>
    <tr>
      <td>m3x12 screw</td>
      <td>10</td>
      <td></td>
    </tr>
    <tr>
      <td>m3x16 screw</td>
      <td>18</td>
      <td></td>
    </tr>
    <tr>
      <td>m3x25 screw</td>
      <td>11</td>
      <td></td>
    </tr>
    <tr>
      <td>m3x35 screw</td>
      <td>6</td>
      <td></td>
    </tr>
    <tr>
      <td>m3x40 screw</td>
      <td>8</td>
      <td></td>
    </tr>
  </tbody>
</table>

## Details

#### Frame Back Left
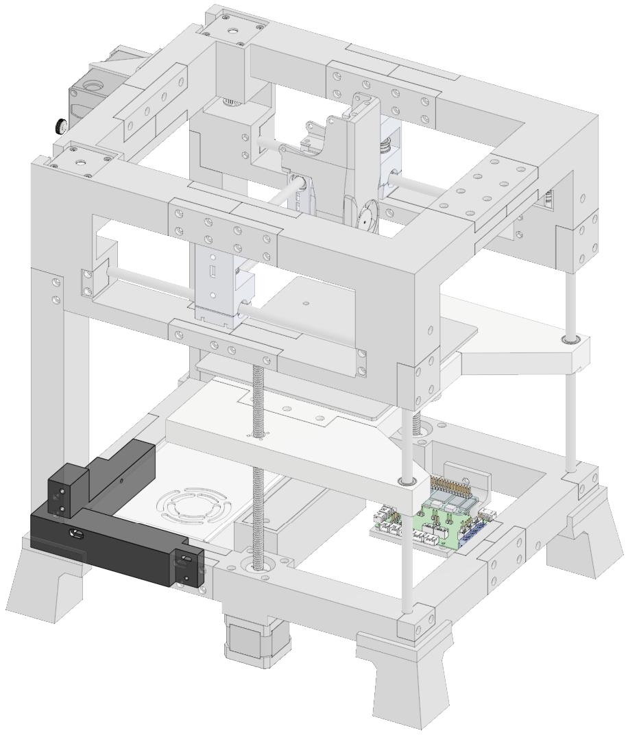
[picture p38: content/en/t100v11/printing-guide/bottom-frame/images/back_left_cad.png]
  
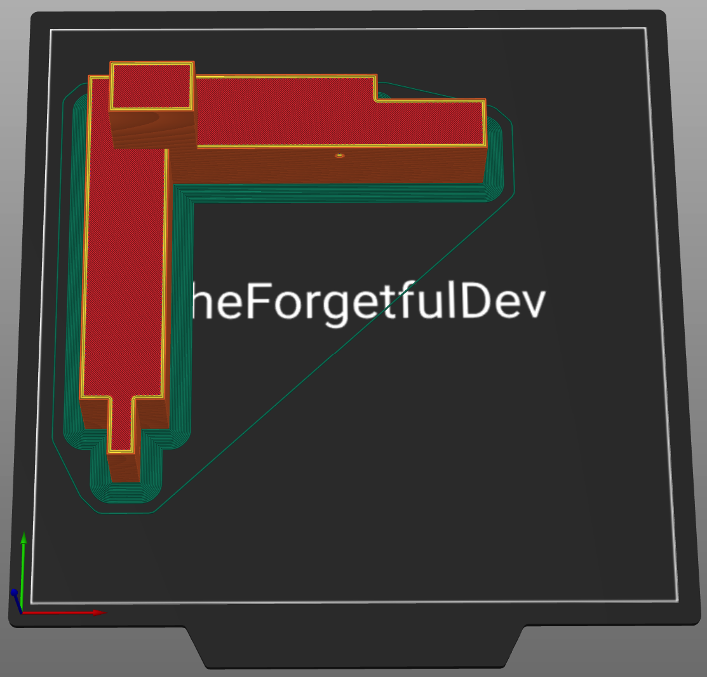
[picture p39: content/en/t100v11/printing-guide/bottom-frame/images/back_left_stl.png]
  
##### Print
<table class="table table-striped table-hover no-margin">
  <tbody class="table-group-divider">
    <tr>
      <th scope="row" class="no-wrap">Quantity</th>
      <td> </td>
      <td>1</td>
    </tr>
    <tr>
      <th scope="row" class="no-wrap">Filament Length</th>
      <td> </td>
      <td>41m</td>
    </tr>
    <tr>
      <th scope="row" class="no-wrap">Filament Weight</th>
      <td> </td>
      <td>122.2g</td>
    </tr>
    <tr>
      <th scope="row" class="no-wrap">Supports?</th>
      <td> </td>
      <td>No</td>
    </tr>
    <tr>
      <th scope="row" class="no-wrap">Notes</th>
      <td> </td>
      <td>A brim is recommended to prevent warping.</td>
    </tr>
  </tbody>
</table>

##### Purchase
<table class="table table-striped table-hover no-margin">
  <thead>
    <tr>
      <th scope="col">Item</th>
      <th scope="col">Qty</th>
      <th scope="col">Note</th>
    </tr>
  </thead>
  <tbody>
    <tr>
      <td>m3 heat insert</td>
      <td>12</td>
      <td></td>
    </tr>
    <tr>
      <td>m3x35 screw</td>
      <td>2</td>
      <td>For holding the PSU</td>
    </tr>
  </tbody>
</table>

#### Frame Back Right
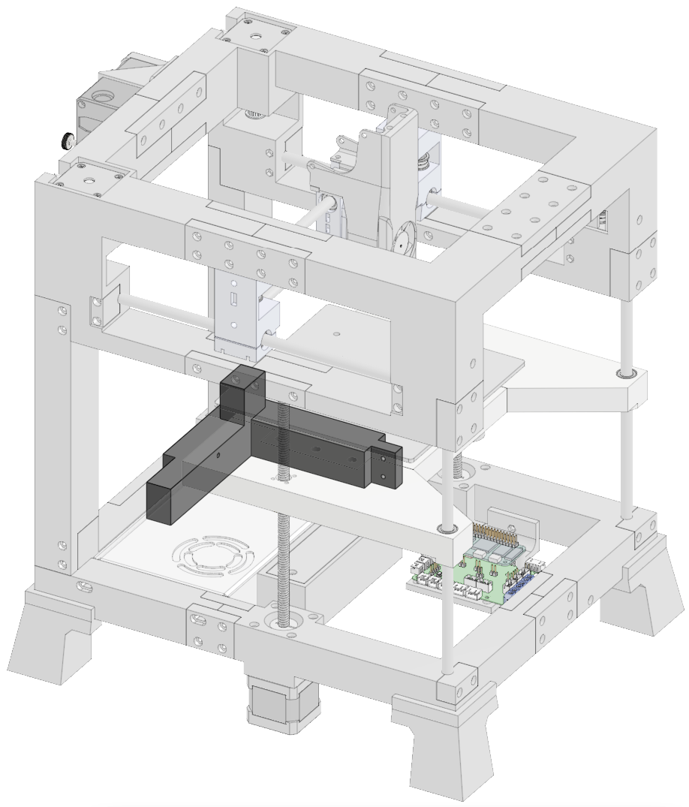
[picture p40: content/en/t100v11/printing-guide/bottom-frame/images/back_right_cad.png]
  
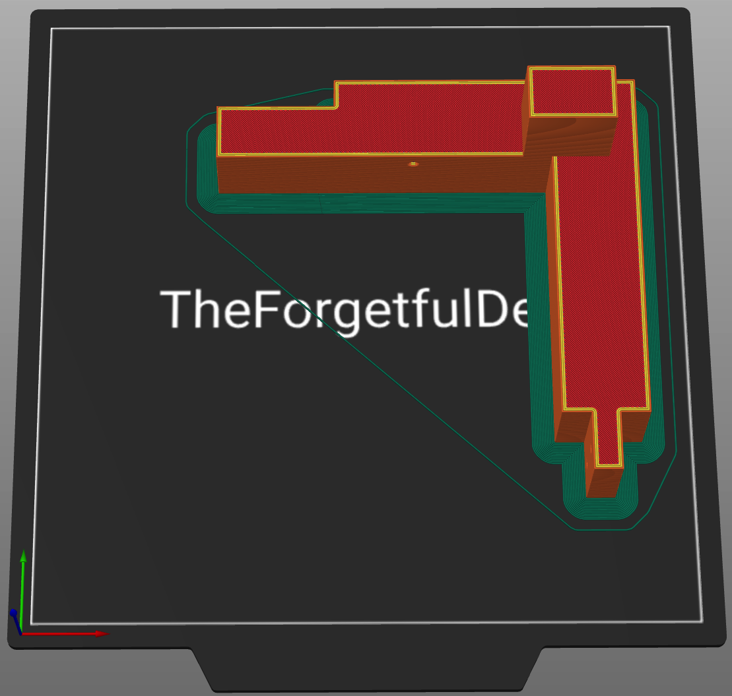
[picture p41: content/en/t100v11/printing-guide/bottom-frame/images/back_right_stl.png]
  
##### Print
<table class="table table-striped table-hover no-margin">
  <tbody class="table-group-divider">
    <tr>
      <th scope="row" class="no-wrap">Quantity</th>
      <td> </td>
      <td>1</td>
    </tr>
    <tr>
      <th scope="row" class="no-wrap">Filament Length</th>
      <td> </td>
      <td>40.9m</td>
    </tr>
    <tr>
      <th scope="row" class="no-wrap">Filament Weight</th>
      <td> </td>
      <td>121.9g</td>
    </tr>
    <tr>
      <th scope="row" class="no-wrap">Supports?</th>
      <td> </td>
      <td>No</td>
    </tr>
    <tr>
      <th scope="row" class="no-wrap">Notes</th>
      <td> </td>
      <td>A brim is recommended to prevent warping.</td>
    </tr>
  </tbody>
</table>

##### Purchase
<table class="table table-striped table-hover no-margin">
  <thead>
    <tr>
      <th scope="col">Item</th>
      <th scope="col">Qty</th>
      <th scope="col">Note</th>
    </tr>
  </thead>
  <tbody>
    <tr>
      <td>m3 heat insert</td>
      <td>14</td>
      <td></td>
    </tr>
    <tr>
      <td>m3x35 screw</td>
      <td>1</td>
      <td>For holding the PSU</td>
    </tr>
  </tbody>
</table>

#### Frame Front Left
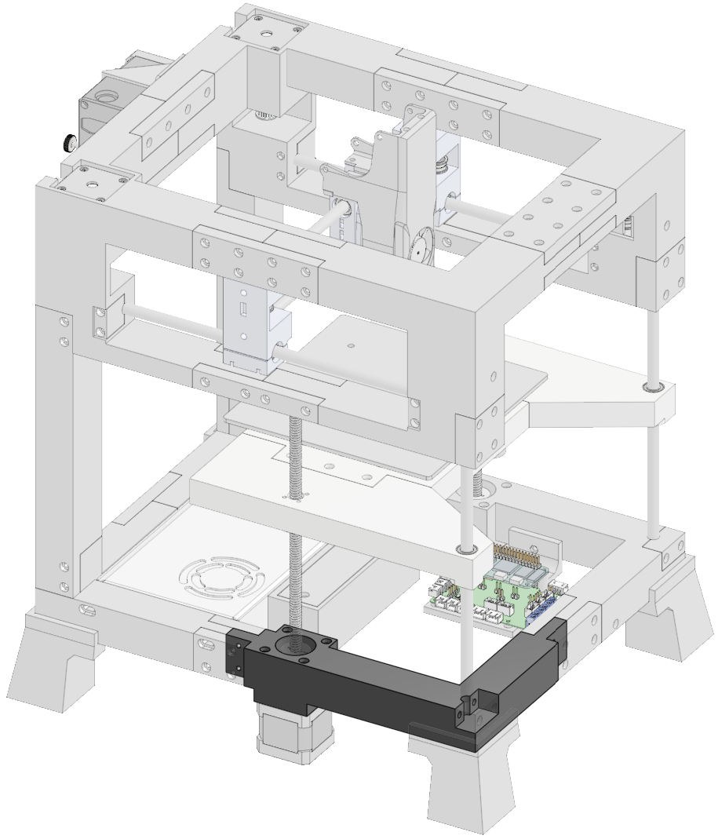
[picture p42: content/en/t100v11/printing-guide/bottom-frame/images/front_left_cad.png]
  
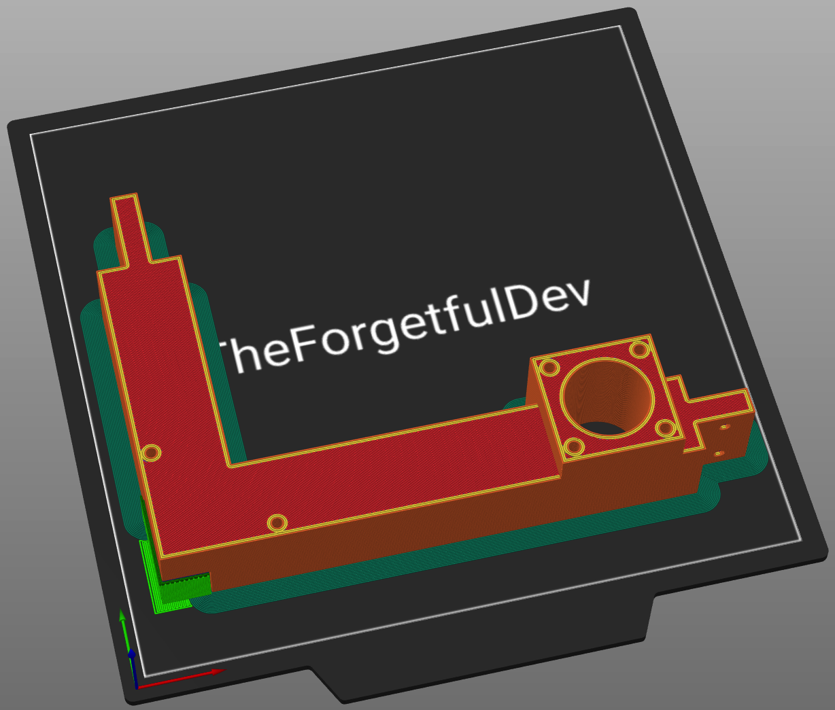
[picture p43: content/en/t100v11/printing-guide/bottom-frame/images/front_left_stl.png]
  
##### Print
<table class="table table-striped table-hover no-margin">
  <tbody class="table-group-divider">
    <tr>
      <th scope="row" class="no-wrap">Quantity</th>
      <td> </td>
      <td>1</td>
    </tr>
    <tr>
      <th scope="row" class="no-wrap">Filament Length</th>
      <td> </td>
      <td>51.1m</td>
    </tr>
    <tr>
      <th scope="row" class="no-wrap">Filament Weight</th>
      <td> </td>
      <td>152.5g</td>
    </tr>
    <tr>
      <th scope="row" class="no-wrap">Supports?</th>
      <td> </td>
      <td>Yes</td>
    </tr>
    <tr>
      <th scope="row" class="no-wrap">Notes</th>
      <td> </td>
      <td>A brim is recommended to prevent warping.</td>
    </tr>
  </tbody>
</table>

##### Purchase
<table class="table table-striped table-hover no-margin">
  <thead>
    <tr>
      <th scope="col">Item</th>
      <th scope="col">Qty</th>
      <th scope="col">Note</th>
    </tr>
  </thead>
  <tbody>
    <tr>
      <td>m3 heat insert</td>
      <td>4</td>
      <td></td>
    </tr>
    <tr>
      <td>m3x40 screw</td>
      <td>4</td>
      <td>For holding the motor</td>
    </tr>
  </tbody>
</table>

#### Frame Front Right
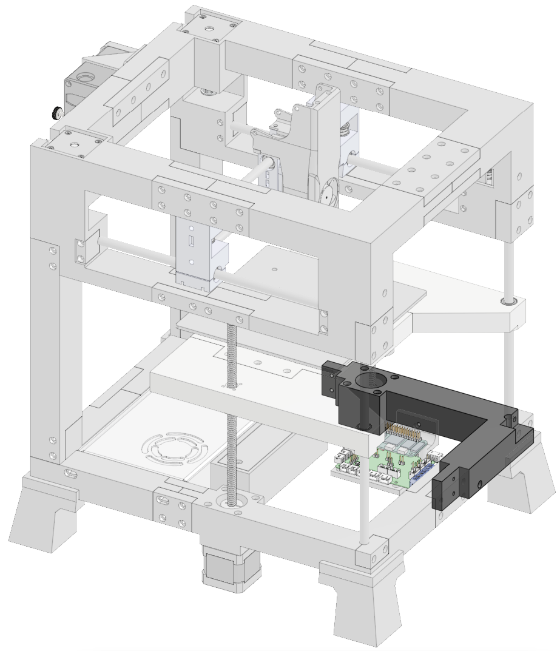
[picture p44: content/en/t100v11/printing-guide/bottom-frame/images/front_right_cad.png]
  
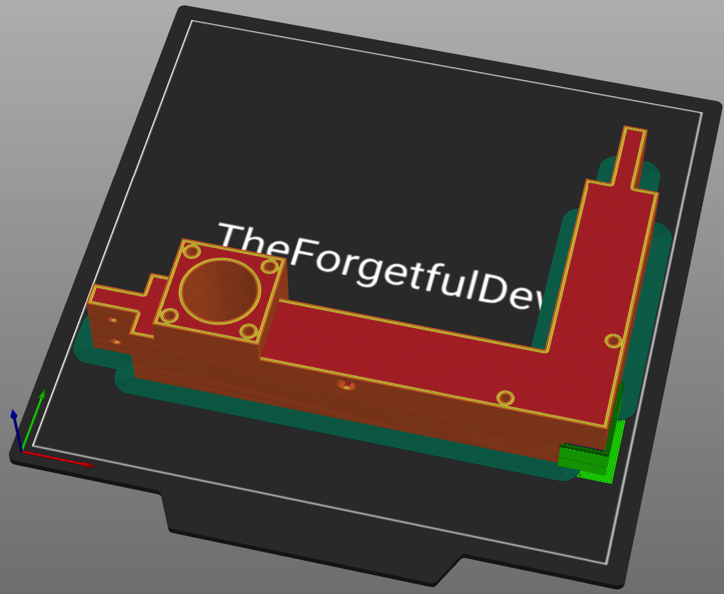
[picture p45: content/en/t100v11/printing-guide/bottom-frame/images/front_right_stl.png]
  
##### Print
<table class="table table-striped table-hover no-margin">
  <tbody class="table-group-divider">
    <tr>
      <th scope="row" class="no-wrap">Quantity</th>
      <td> </td>
      <td>1</td>
    </tr>
    <tr>
      <th scope="row" class="no-wrap">Filament Length</th>
      <td> </td>
      <td>51.8m</td>
    </tr>
    <tr>
      <th scope="row" class="no-wrap">Filament Weight</th>
      <td> </td>
      <td>154.6g</td>
    </tr>
    <tr>
      <th scope="row" class="no-wrap">Supports?</th>
      <td> </td>
      <td>Yes</td>
    </tr>
    <tr>
      <th scope="row" class="no-wrap">Notes</th>
      <td> </td>
      <td>A brim is recommended to prevent warping.</td>
    </tr>
  </tbody>
</table>

##### Purchase
<table class="table table-striped table-hover no-margin">
  <thead>
    <tr>
      <th scope="col">Item</th>
      <th scope="col">Qty</th>
      <th scope="col">Note</th>
    </tr>
  </thead>
  <tbody>
    <tr>
      <td>m3 heat insert</td>
      <td>4</td>
      <td></td>
    </tr>
    <tr>
      <td>m3x40 screw</td>
      <td>4</td>
      <td>For holding the motor</td>
    </tr>
    <tr>
      <td>m3x35 screw</td>
      <td>2</td>
      <td>For holding the mainboard tray</td>
    </tr>
  </tbody>
</table>

#### Frame Connector Back
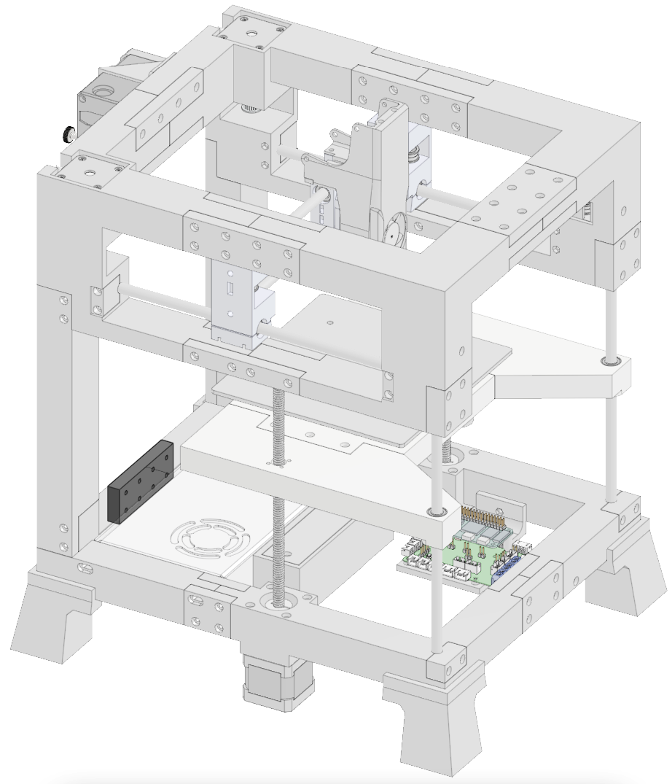
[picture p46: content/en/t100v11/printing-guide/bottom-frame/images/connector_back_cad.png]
  
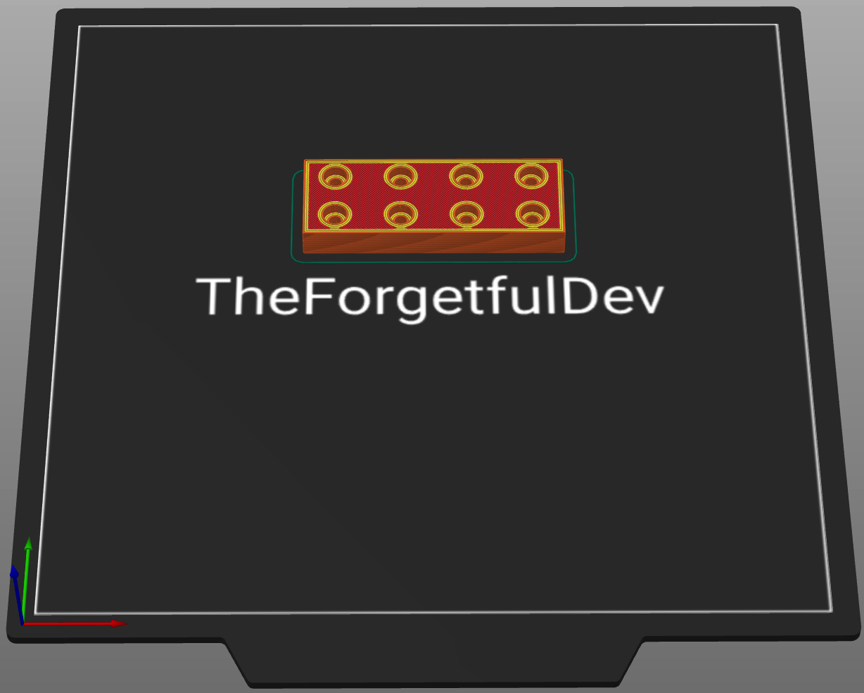
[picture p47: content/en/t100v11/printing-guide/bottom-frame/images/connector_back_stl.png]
  
##### Print
<table class="table table-striped table-hover no-margin">
  <tbody class="table-group-divider">
    <tr>
      <th scope="row" class="no-wrap">Quantity</th>
      <td> </td>
      <td>1</td>
    </tr>
    <tr>
      <th scope="row" class="no-wrap">Filament Length</th>
      <td> </td>
      <td>5.5m</td>
    </tr>
    <tr>
      <th scope="row" class="no-wrap">Filament Weight</th>
      <td> </td>
      <td>16.5g</td>
    </tr>
    <tr>
      <th scope="row" class="no-wrap">Supports?</th>
      <td> </td>
      <td>No</td>
    </tr>
  </tbody>
</table>

##### Hardware
<table class="table table-sm no-margin">
  <thead>
    <tr>
      <th scope="col">Item</th>
      <th scope="col">Qty</th>
      <th scope="col">Note</th>
    </tr>
  </thead>
  <tbody>
    <tr>
      <td>m3x12 screw</td>
      <td>8</td>
      <td></td>
    </tr>
  </tbody>
</table>

#### Frame Connector Front 2
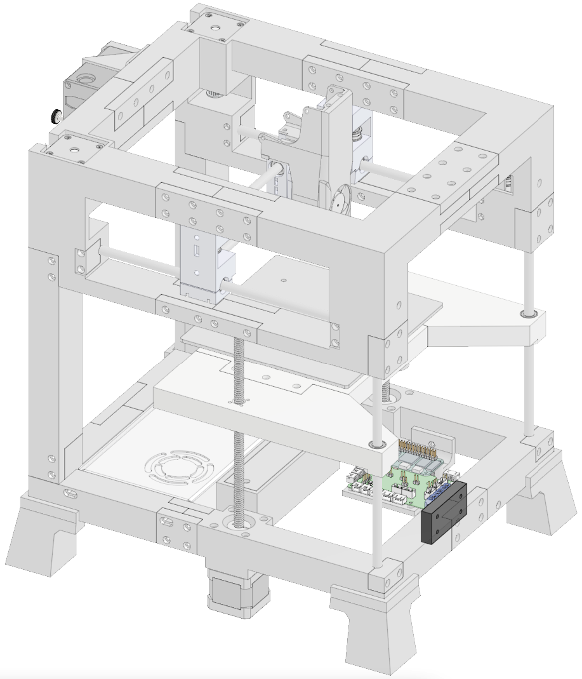
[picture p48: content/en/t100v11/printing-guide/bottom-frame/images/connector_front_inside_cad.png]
  
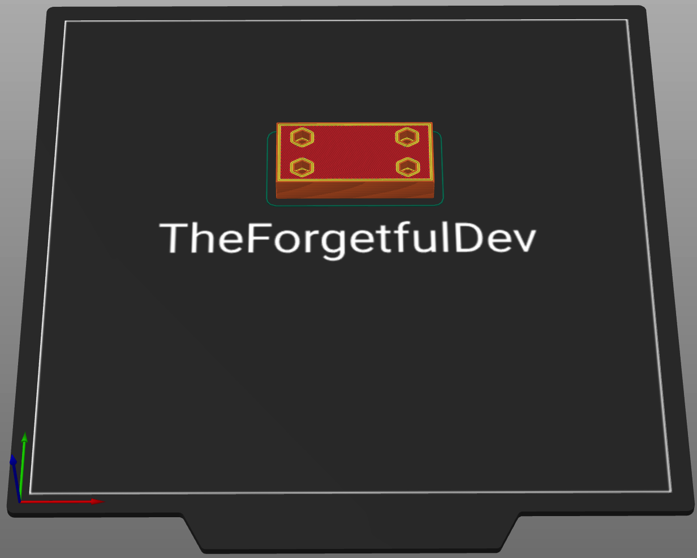
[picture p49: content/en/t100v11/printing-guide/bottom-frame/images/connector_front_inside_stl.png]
  
##### Print
<table class="table table-striped table-hover no-margin">
  <tbody class="table-group-divider">
    <tr>
      <th scope="row" class="no-wrap">Quantity</th>
      <td> </td>
      <td>1</td>
    </tr>
    <tr>
      <th scope="row" class="no-wrap">Filament Length</th>
      <td> </td>
      <td>4.2m</td>
    </tr>
    <tr>
      <th scope="row" class="no-wrap">Filament Weight</th>
      <td> </td>
      <td>12.4g</td>
    </tr>
    <tr>
      <th scope="row" class="no-wrap">Supports?</th>
      <td> </td>
      <td>No</td>
    </tr>
    <tr>
      <th scope="row" class="no-wrap">Notes</th>
      <td> </td>
      <td>Uses inset nuts rather than heat inserts</td>
    </tr>
  </tbody>
</table>

##### Hardware
<table class="table table-sm no-margin">
  <thead>
    <tr>
      <th scope="col">Item</th>
      <th scope="col">Qty</th>
      <th scope="col">Note</th>
    </tr>
  </thead>
  <tbody>
    <tr>
      <td>m3 nut</td>
      <td>4</td>
      <td></td>
    </tr>
  </tbody>
</table>

#### Frame Connector Front 1
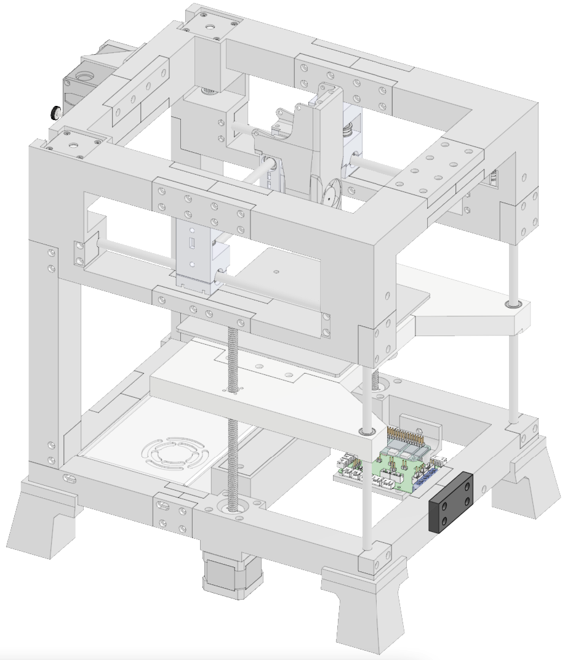
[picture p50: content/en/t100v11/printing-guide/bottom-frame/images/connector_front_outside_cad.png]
  
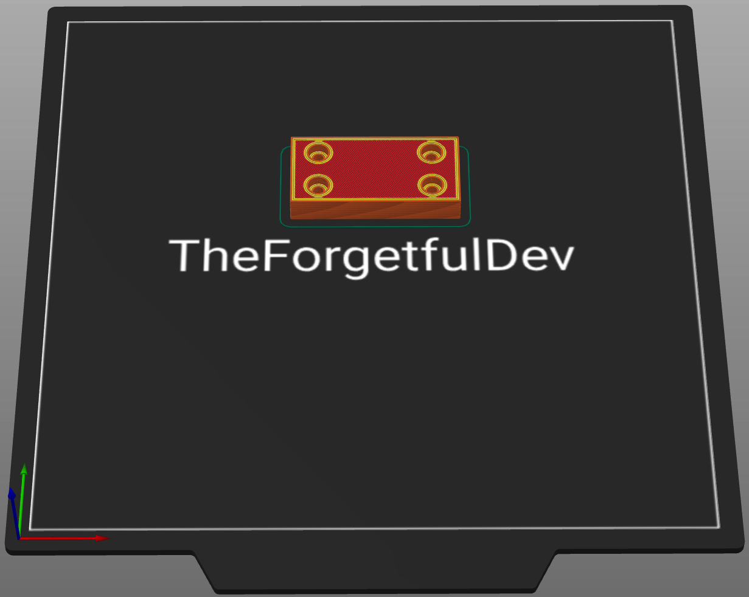
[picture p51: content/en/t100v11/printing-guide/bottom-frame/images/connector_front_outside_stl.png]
  
##### Print
<table class="table table-striped table-hover no-margin">
  <tbody class="table-group-divider">
    <tr>
      <th scope="row" class="no-wrap">Quantity</th>
      <td> </td>
      <td>1</td>
    </tr>
    <tr>
      <th scope="row" class="no-wrap">Filament Length</th>
      <td> </td>
      <td>4.1m</td>
    </tr>
    <tr>
      <th scope="row" class="no-wrap">Filament Weight</th>
      <td> </td>
      <td>12.3g</td>
    </tr>
    <tr>
      <th scope="row" class="no-wrap">Supports?</th>
      <td> </td>
      <td>No</td>
    </tr>
  </tbody>
</table>

##### Hardware
<table class="table table-sm no-margin">
  <thead>
    <tr>
      <th scope="col">Item</th>
      <th scope="col">Qty</th>
      <th scope="col">Note</th>
    </tr>
  </thead>
  <tbody>
    <tr>
      <td>m3x25 screw</td>
      <td>4</td>
      <td>m3x30 also works but will stick out slightly</td>
    </tr>
  </tbody>
</table>

#### Frame Connector Left 1
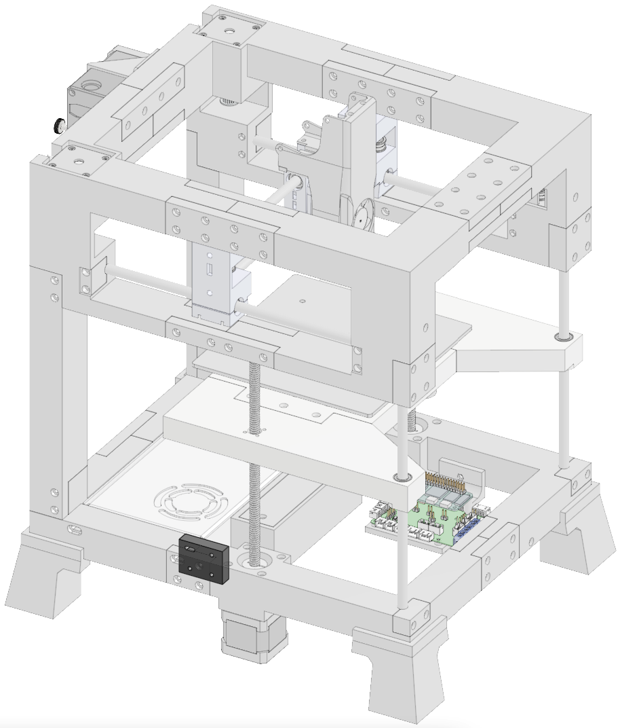
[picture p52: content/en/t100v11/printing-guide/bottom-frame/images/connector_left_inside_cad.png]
  
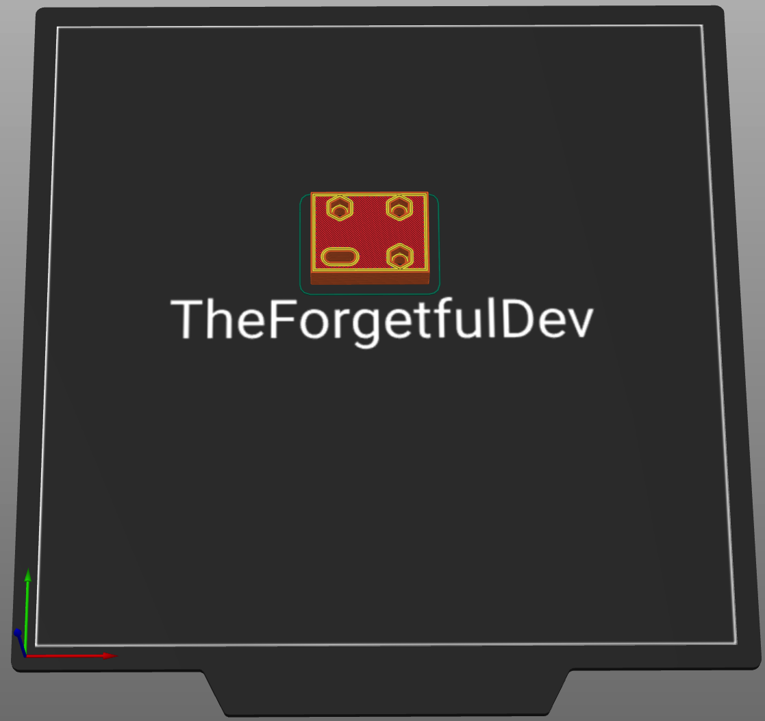
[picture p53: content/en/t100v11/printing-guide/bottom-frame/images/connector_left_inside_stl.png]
  
##### Print
<table class="table table-striped table-hover no-margin">
  <tbody class="table-group-divider">
    <tr>
      <th scope="row" class="no-wrap">Quantity</th>
      <td> </td>
      <td>1</td>
    </tr>
    <tr>
      <th scope="row" class="no-wrap">Filament Length</th>
      <td> </td>
      <td>3m</td>
    </tr>
    <tr>
      <th scope="row" class="no-wrap">Filament Weight</th>
      <td> </td>
      <td>8.9g</td>
    </tr>
    <tr>
      <th scope="row" class="no-wrap">Supports?</th>
      <td> </td>
      <td>No</td>
    </tr>
    <tr>
      <th scope="row" class="no-wrap">Notes</th>
      <td> </td>
      <td>Uses inset nuts rather than heat inserts</td>
    </tr>
  </tbody>
</table>

##### Hardware
<table class="table table-sm no-margin">
  <thead>
    <tr>
      <th scope="col">Item</th>
      <th scope="col">Qty</th>
      <th scope="col">Note</th>
    </tr>
  </thead>
  <tbody>
    <tr>
      <td>m3 nut</td>
      <td>3</td>
      <td></td>
    </tr>
  </tbody>
</table>

#### Frame Connector Left 2
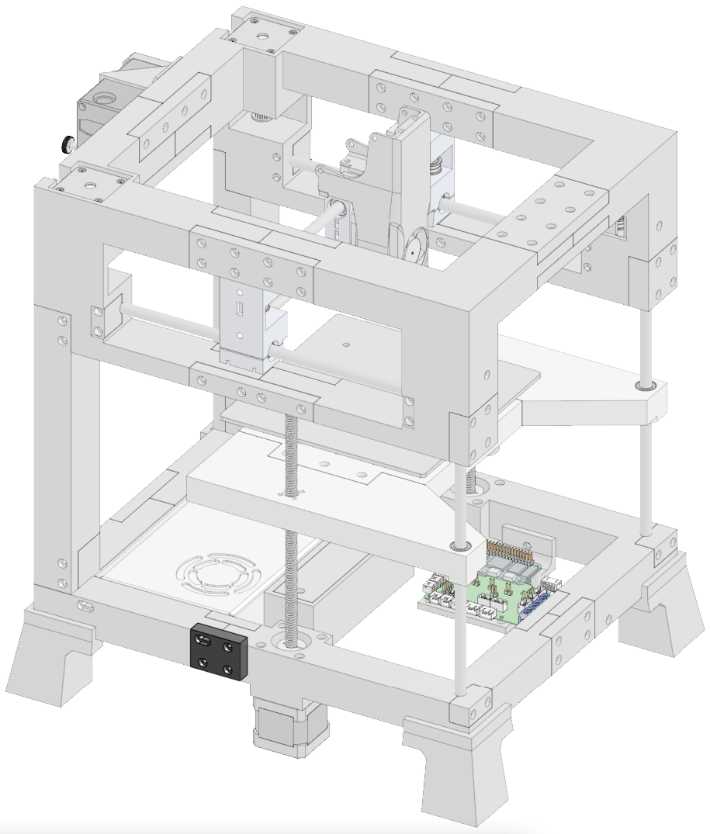
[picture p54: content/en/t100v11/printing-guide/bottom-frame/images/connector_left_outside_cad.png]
  
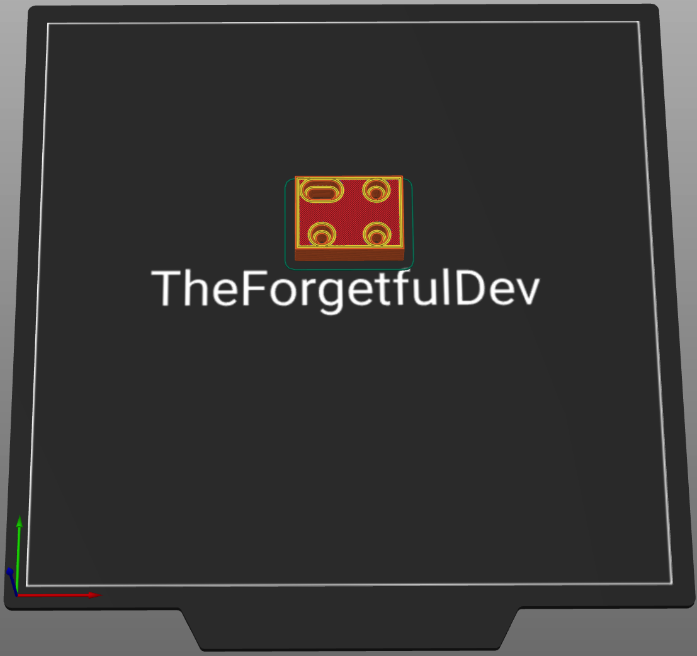
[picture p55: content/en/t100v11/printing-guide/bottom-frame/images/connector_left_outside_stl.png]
  
##### Print
<table class="table table-striped table-hover no-margin">
  <tbody class="table-group-divider">
    <tr>
      <th scope="row" class="no-wrap">Quantity</th>
      <td> </td>
      <td>1</td>
    </tr>
    <tr>
      <th scope="row" class="no-wrap">Filament Length</th>
      <td> </td>
      <td>2.9m</td>
    </tr>
    <tr>
      <th scope="row" class="no-wrap">Filament Weight</th>
      <td> </td>
      <td>8.8g</td>
    </tr>
    <tr>
      <th scope="row" class="no-wrap">Supports?</th>
      <td> </td>
      <td>No</td>
    </tr>
  </tbody>
</table>

##### Hardware
<table class="table table-sm no-margin">
  <thead>
    <tr>
      <th scope="col">Item</th>
      <th scope="col">Qty</th>
      <th scope="col">Note</th>
    </tr>
  </thead>
  <tbody>
    <tr>
      <td>m3x25 screw</td>
      <td>3</td>
      <td></td>
    </tr>
    <tr>
      <td>m3x35 screw</td>
      <td>1</td>
      <td>Oval hole for PSU</td>
    </tr>
  </tbody>
</table>

#### Frame Connector Right 1
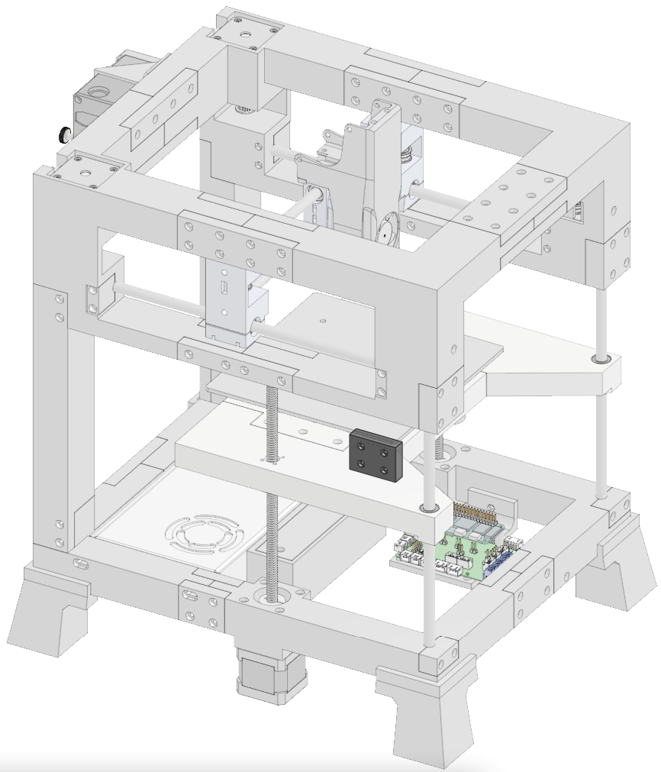
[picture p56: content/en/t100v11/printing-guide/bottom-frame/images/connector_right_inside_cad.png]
  
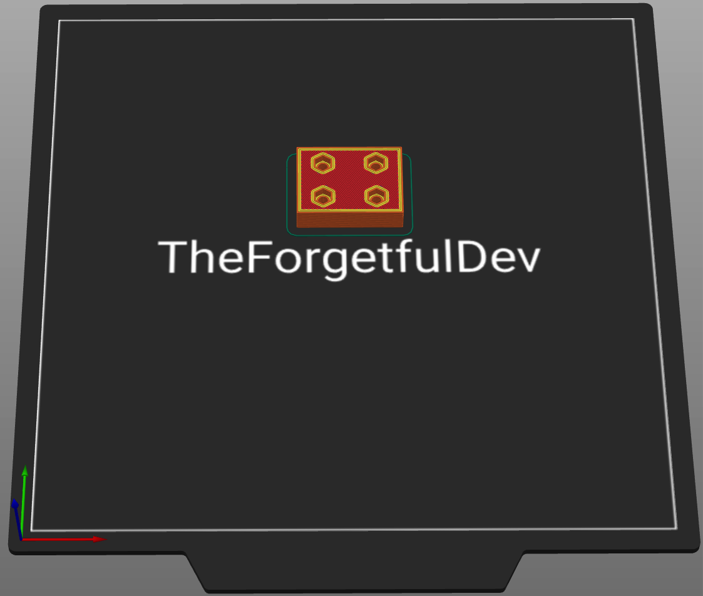
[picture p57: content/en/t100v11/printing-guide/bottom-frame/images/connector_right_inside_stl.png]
  
##### Print
<table class="table table-striped table-hover no-margin">
  <tbody class="table-group-divider">
    <tr>
      <th scope="row" class="no-wrap">Quantity</th>
      <td> </td>
      <td>1</td>
    </tr>
    <tr>
      <th scope="row" class="no-wrap">Filament Length</th>
      <td> </td>
      <td>2.9m</td>
    </tr>
    <tr>
      <th scope="row" class="no-wrap">Filament Weight</th>
      <td> </td>
      <td>8.7g</td>
    </tr>
    <tr>
      <th scope="row" class="no-wrap">Supports?</th>
      <td> </td>
      <td>No</td>
    </tr>
    <tr>
      <th scope="row" class="no-wrap">Notes</th>
      <td> </td>
      <td>Uses inset nuts rather than heat inserts</td>
    </tr>
  </tbody>
</table>

##### Hardware
<table class="table table-sm no-margin">
  <thead>
    <tr>
      <th scope="col">Item</th>
      <th scope="col">Qty</th>
      <th scope="col">Note</th>
    </tr>
  </thead>
  <tbody>
    <tr>
      <td>m3 nut</td>
      <td>4</td>
      <td></td>
    </tr>
  </tbody>
</table>

#### Frame Connector Right 2
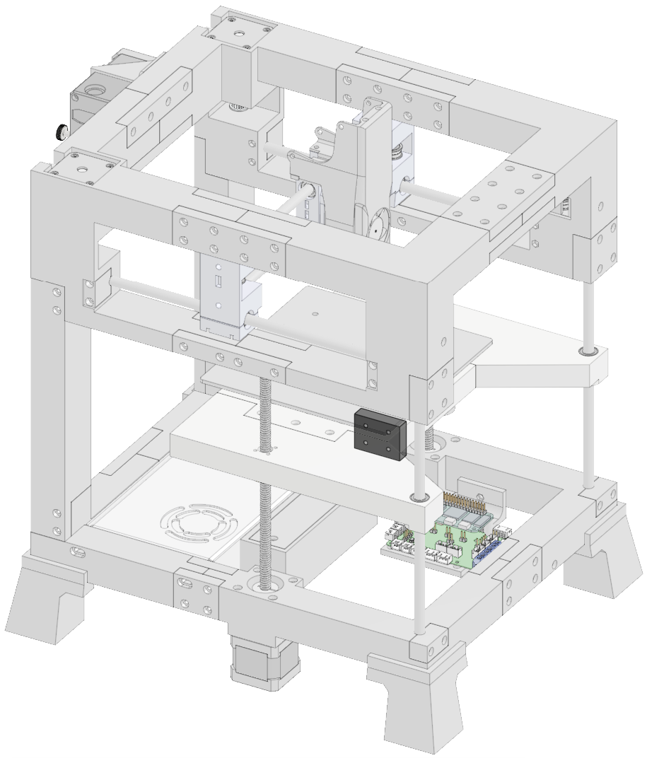
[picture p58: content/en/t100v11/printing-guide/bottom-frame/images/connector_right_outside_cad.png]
  
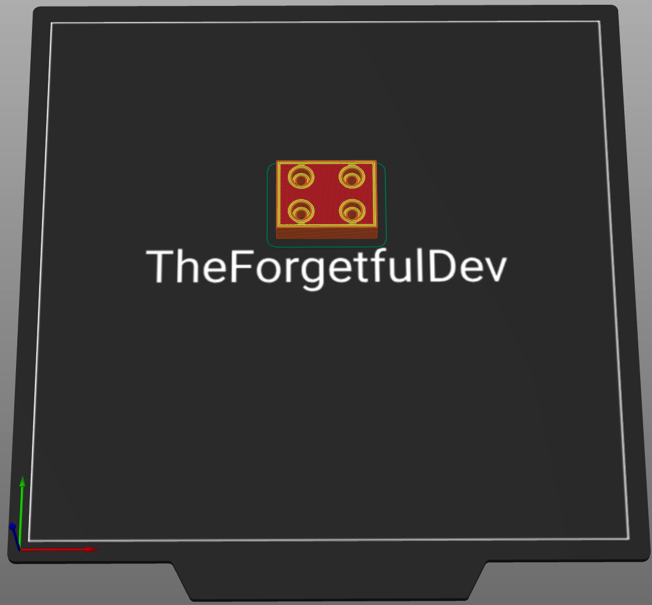
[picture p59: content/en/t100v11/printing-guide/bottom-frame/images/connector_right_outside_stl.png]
  
##### Print
<table class="table table-striped table-hover no-margin">
  <tbody class="table-group-divider">
    <tr>
      <th scope="row" class="no-wrap">Quantity</th>
      <td> </td>
      <td>1</td>
    </tr>
    <tr>
      <th scope="row" class="no-wrap">Filament Length</th>
      <td> </td>
      <td>2.9m</td>
    </tr>
    <tr>
      <th scope="row" class="no-wrap">Filament Weight</th>
      <td> </td>
      <td>8.7g</td>
    </tr>
    <tr>
      <th scope="row" class="no-wrap">Supports?</th>
      <td> </td>
      <td>No</td>
    </tr>
  </tbody>
</table>

##### Hardware
<table class="table table-sm no-margin">
  <thead>
    <tr>
      <th scope="col">Item</th>
      <th scope="col">Qty</th>
      <th scope="col">Note</th>
    </tr>
  </thead>
  <tbody>
    <tr>
      <td>m3x25 screw</td>
      <td>4</td>
      <td>m3x30 also works but will stick out slightly</td>
    </tr>
  </tbody>
</table>

#### Foot
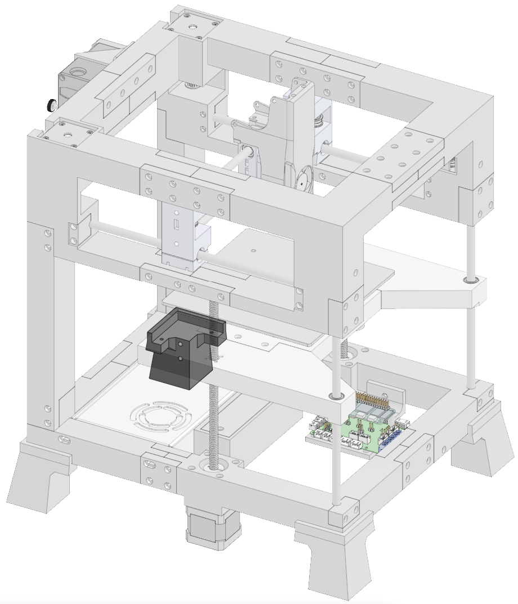
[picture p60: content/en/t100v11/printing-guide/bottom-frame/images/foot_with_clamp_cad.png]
  
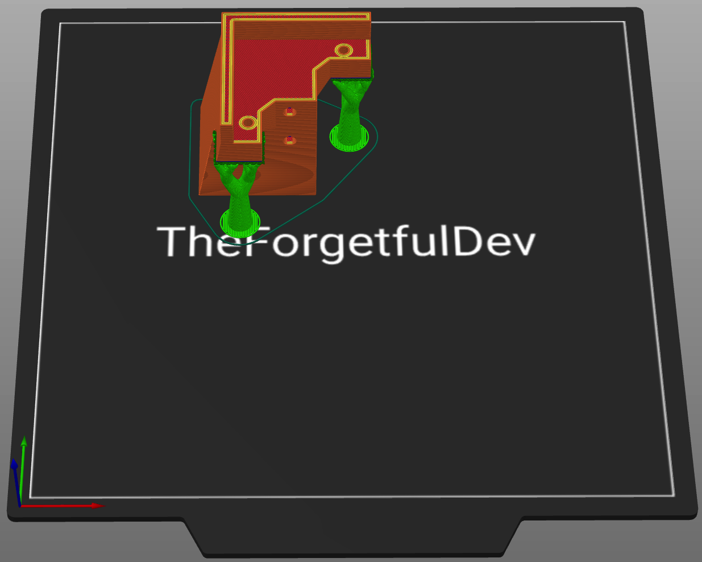
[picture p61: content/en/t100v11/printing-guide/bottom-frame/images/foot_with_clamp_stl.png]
  
##### Print
<table class="table table-striped table-hover no-margin">
  <tbody class="table-group-divider">
    <tr>
      <th scope="row" class="no-wrap">Quantity</th>
      <td> </td>
      <td>4</td>
    </tr>
    <tr>
      <th scope="row" class="no-wrap">Filament Length</th>
      <td> </td>
      <td>19.6m</td>
    </tr>
    <tr>
      <th scope="row" class="no-wrap">Filament Weight</th>
      <td> </td>
      <td>58.4g</td>
    </tr>
    <tr>
      <th scope="row" class="no-wrap">Supports?</th>
      <td> </td>
      <td>Yes - Using organic supports is smart here if your slicer supports them. It isn't necessary but will use 3g of material for supports instead of 11g. </td>
    </tr>
    <tr>
      <th scope="row" class="no-wrap">Notes</th>
      <td> </td>
      <td>The back right foot has a spot for 2 heat inserts for a clamp that holds the power supply cable. I personally printed that foot 4x and just don't put the heat inserts in the other 3 feet but you can choose to print just 1 with the holes and the other 3 without. The version without the extra mounting holes can be found here: <a target="_blank" href="https://github.com/MSzturc/t100/blob/main/STL/Bottom%20Frame/Foot%20Back%20Left.stl">github</a> / <a href="https://files.printables.com/media/prints/572689/stls/4581573_c9d87696-653e-410f-970e-556d52263bc1/foot-back-left.stl">printables</a>.</td>
    </tr>
  </tbody>
</table>

##### Hardware
<table class="table table-sm no-margin">
  <thead>
    <tr>
      <th scope="col">Item</th>
      <th scope="col">Qty</th>
      <th scope="col">Note</th>
    </tr>
  </thead>
  <tbody>
    <tr>
      <td>m3 heat insert</td>
      <td>2</td>
      <td>For the back right foot only</td>
    </tr>
    <tr>
      <td>m3x16 screw</td>
      <td>2</td>
      <td>Put a washer on it before attaching</td>
    </tr>
    <tr>
      <td>m3 washer</td>
      <td>2</td>
      <td></td>
    </tr>
  </tbody>
</table>

#### 5mm - 8mm Coupler
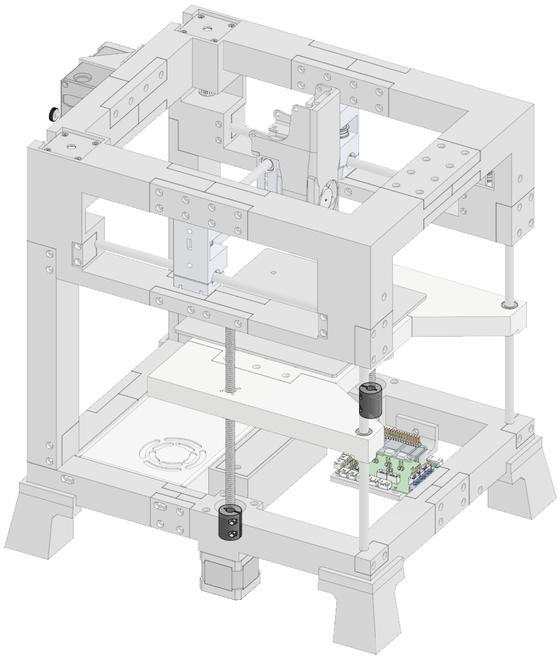
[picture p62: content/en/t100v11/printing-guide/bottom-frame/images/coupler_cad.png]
  
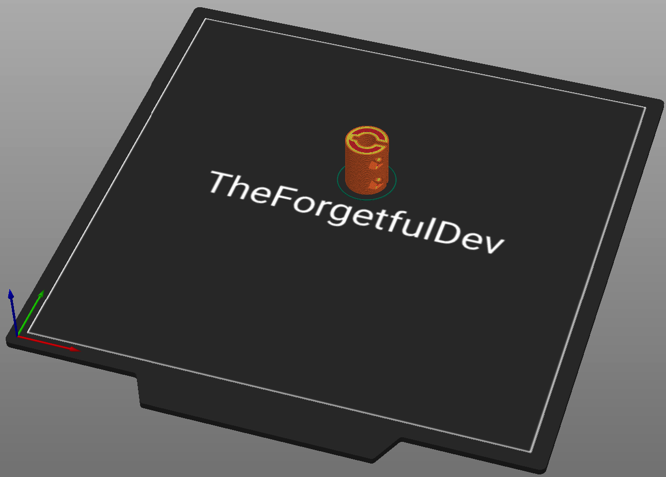
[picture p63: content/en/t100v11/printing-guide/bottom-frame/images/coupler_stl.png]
  
##### Print
<table class="table table-striped table-hover no-margin">
  <tbody class="table-group-divider">
    <tr>
      <th scope="row" class="no-wrap">Quantity</th>
      <td> </td>
      <td>2</td>
    </tr>
    <tr>
      <th scope="row" class="no-wrap">Filament Length</th>
      <td> </td>
      <td>2.1m</td>
    </tr>
    <tr>
      <th scope="row" class="no-wrap">Filament Weight</th>
      <td> </td>
      <td>6.4g</td>
    </tr>
    <tr>
      <th scope="row" class="no-wrap">Supports?</th>
      <td> </td>
      <td>No</td>
    </tr>
    <tr>
      <th scope="row" class="no-wrap">Notes</th>
      <td> </td>
      <td>This is a necessary part if you didn't purchase them. These allow you to connect the screw rod to the motor. I printed mine in petg but that's mainly because it was already loaded in my printer. I think PLA is perfectly fine for this part. </td>
    </tr>
  </tbody>
</table>

##### Hardware
<table class="table table-sm no-margin">
  <thead>
    <tr>
      <th scope="col">Item</th>
      <th scope="col">Qty</th>
      <th scope="col">Note</th>
    </tr>
  </thead>
  <tbody>
    <tr>
      <td>m3 nut</td>
      <td>2</td>
      <td></td>
    </tr>
    <tr>
      <td>m3x12mm screw</td>
      <td>2</td>
      <td></td>
    </tr>
  </tbody>
</table>

#### Connector Z-Rod
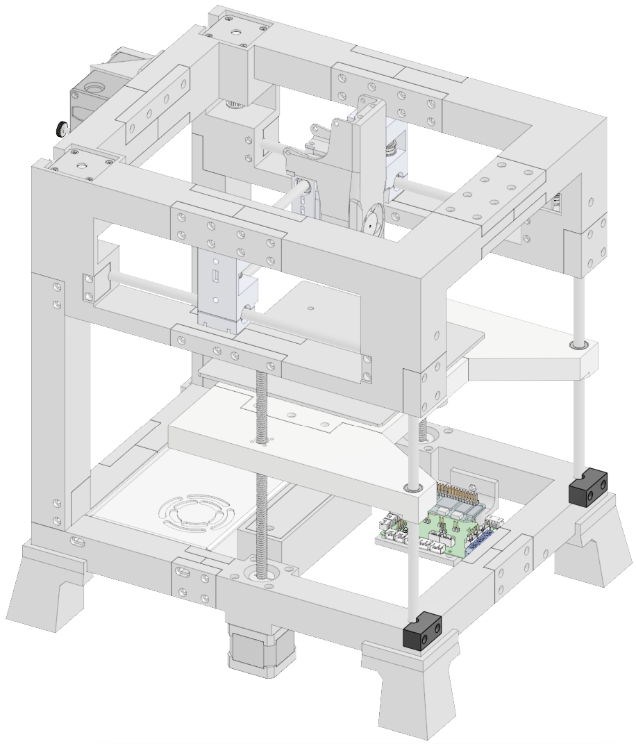
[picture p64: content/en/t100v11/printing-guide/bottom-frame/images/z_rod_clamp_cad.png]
  
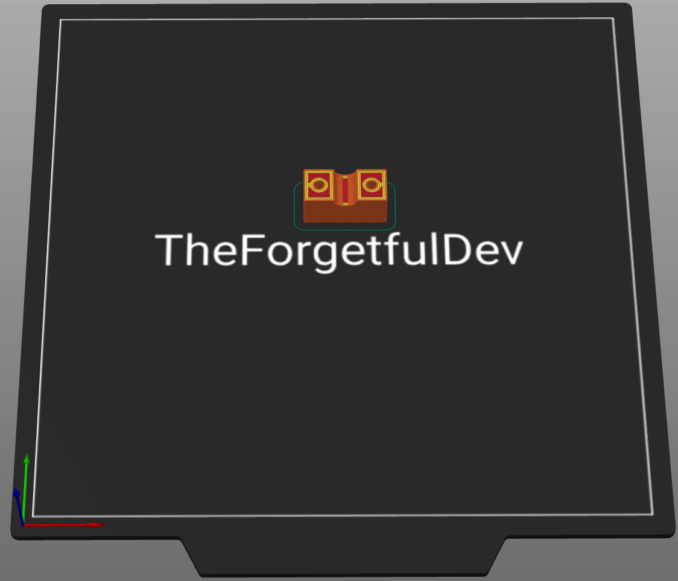
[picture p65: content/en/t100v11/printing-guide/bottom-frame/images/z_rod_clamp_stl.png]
  
##### Print
<table class="table table-striped table-hover no-margin">
  <tbody class="table-group-divider">
    <tr>
      <th scope="row" class="no-wrap">Quantity</th>
      <td> </td>
      <td>2</td>
    </tr>
    <tr>
      <th scope="row" class="no-wrap">Filament Length</th>
      <td> </td>
      <td>2m</td>
    </tr>
    <tr>
      <th scope="row" class="no-wrap">Filament Weight</th>
      <td> </td>
      <td>6g</td>
    </tr>
    <tr>
      <th scope="row" class="no-wrap">Supports?</th>
      <td> </td>
      <td>Yes - only in the countersunk holes touching the buildplate</td>
    </tr>
  </tbody>
</table>

##### Hardware
<table class="table table-sm no-margin">
  <thead>
    <tr>
      <th scope="col">Item</th>
      <th scope="col">Qty</th>
      <th scope="col">Note</th>
    </tr>
  </thead>
  <tbody>
    <tr>
      <td>m3x16mm screw</td>
      <td>2</td>
      <td></td>
    </tr>
  </tbody>
</table>

#### Power Cord Clamp
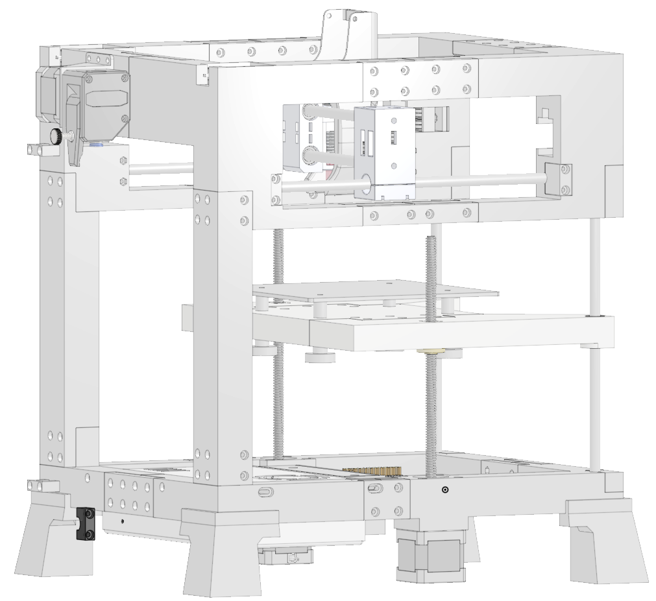
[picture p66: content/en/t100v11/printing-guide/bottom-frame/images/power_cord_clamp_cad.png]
  
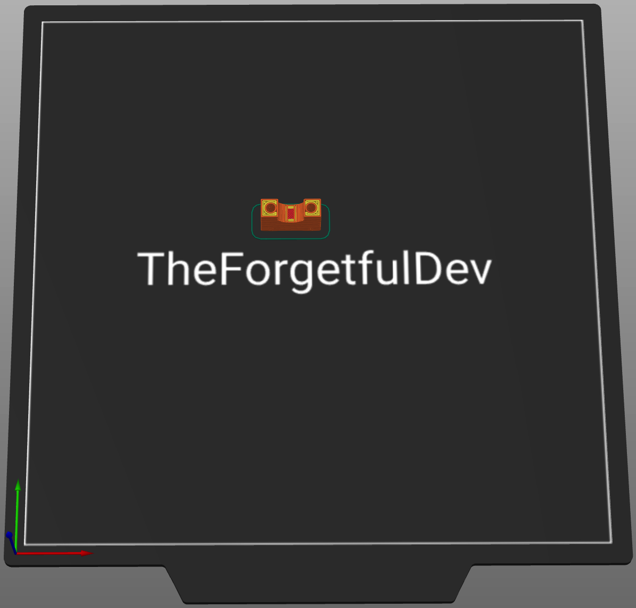
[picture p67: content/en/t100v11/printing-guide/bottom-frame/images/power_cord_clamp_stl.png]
  
##### Print
<table class="table table-striped table-hover no-margin">
  <tbody class="table-group-divider">
    <tr>
      <th scope="row" class="no-wrap">Quantity</th>
      <td> </td>
      <td>1</td>
    </tr>
    <tr>
      <th scope="row" class="no-wrap">Filament Length</th>
      <td> </td>
      <td>0.74</td>
    </tr>
    <tr>
      <th scope="row" class="no-wrap">Filament Weight</th>
      <td> </td>
      <td>2.22g</td>
    </tr>
    <tr>
      <th scope="row" class="no-wrap">Supports?</th>
      <td> </td>
      <td>Yes - only in countersunk holes touching the buildplate</td>
    </tr>
  </tbody>
</table>

##### Purchase
<table class="table table-striped table-hover no-margin">
  <thead>
    <tr>
      <th scope="col">Item</th>
      <th scope="col">Qty</th>
      <th scope="col">Note</th>
    </tr>
  </thead>
  <tbody>
    <tr>
      <td>m3x16 screw</td>
      <td>2</td>
      <td></td>
    </tr>
  </tbody>
</table>

#### Cable Guide Clamp
  
  
##### Print
<table class="table table-striped table-hover no-margin">
  <tbody class="table-group-divider">
    <tr>
      <th scope="row" class="no-wrap">Quantity</th>
      <td> </td>
      <td>2</td>
    </tr>
    <tr>
      <th scope="row" class="no-wrap">Filament Length</th>
      <td> </td>
      <td>0.62</td>
    </tr>
    <tr>
      <th scope="row" class="no-wrap">Filament Weight</th>
      <td> </td>
      <td>1.85g</td>
    </tr>
    <tr>
      <th scope="row" class="no-wrap">Supports?</th>
      <td> </td>
      <td>Yes - only in countersunk holes touching the buildplate</td>
    </tr>
  </tbody>
</table>

##### Purchase
<table class="table table-striped table-hover no-margin">
  <thead>
    <tr>
      <th scope="col">Item</th>
      <th scope="col">Qty</th>
      <th scope="col">Note</th>
    </tr>
  </thead>
  <tbody>
    <tr>
      <td>m3x16 screw</td>
      <td>2</td>
      <td></td>
    </tr>
  </tbody>
</table>

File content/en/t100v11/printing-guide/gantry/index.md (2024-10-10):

---
title: "Gantry"
ogTitle: "Gantry - THE 100 Print Guide"
description: "How to print THE 100's v1.1 gantry, as well as what hardware you need to purchase to build it."
lead: ""
date: 2023-06-18T14:41:39+01:00
draft: false
images: []
type: docs
menu:
  t100v11:
    parent: "printing-guide-the100"
weight: 200
toc: true
doc: t100v11
images: 
  - images/tfd_gantry_preview.png
---
# Gantry

<div class="row bd">
  <div class="col">
      
  </div>
  <div class="col">
    <ul class="list-group">
      <li class="list-group-item d-flex justify-content-between align-items-center">
        <div class="text fw-bold">Printed parts</div>
        <div class="text">4</div>
      </li>
    </ul>
    <br>
    <ul class="list-group">
      <li class="list-group-item d-flex justify-content-between align-items-center">
        <div class="text fw-bold">Purchased parts</div>
        <div class="text">44</div>
      </li>
    </ul>   
    <br>
    <ul class="list-group">
      <li class="list-group-item d-flex justify-content-between align-items-center">
        <div class="text fw-bold">Filament</div>
        <div class="text">30.4m | 90.8g</div>
      </li>
    </ul>   
    <br>
    <ul class="list-group">
      <li class="list-group-item d-flex justify-content-between align-items-center">
        <div class="text fw-bold">Print time</div>
        <div class="text">3h 17m</div>
      </li>
    </ul>   
  </div>
</div>

### Printed parts
<table class="table table-sm">
  <thead>
    <tr>
      <th scope="col">Part Name</th>
      <th scope="col">STL</th>
      <th scope="col">Qty</th>
      <th scope="col">Notes</th>
    </tr>
  </thead>
  <tbody>
    <tr>
      <td>Left Gantry</td>
      <td class="no-wrap"><a target="_blank" href="https://github.com/MSzturc/t100/blob/main/STL/Gantry/Left%20Gantry.stl">github</a> / <a href="https://files.printables.com/media/prints/572689/stls/4581549_00354996-cefb-40e9-bc7f-1838937cf501/left-gantry.stl">printables</a></td>
      <td>1</td>
      <td><a href="#left-gantry">More info</a></td>
    </tr>
    <tr>
      <td>Left Gantry Bottom</td>
      <td class="no-wrap"><a target="_blank" href="https://github.com/MSzturc/t100/blob/main/STL/Gantry/Left%20Gantry%20Bottom.stl">github</a> / <a href="https://files.printables.com/media/prints/572689/stls/4581552_39902278-386f-4236-a312-620a327ffd3a/left-gantry-bottom.stl">printables</a></td>
      <td>1</td>
      <td><a href="#left-gantry-bottom">More info</a></td>
    </tr>
    <tr>
      <td>Right Gantry</td>
      <td class="no-wrap"><a target="_blank" href="https://github.com/MSzturc/t100/blob/main/STL/Gantry/Right%20Gantry.stl">github</a> / <a href="https://files.printables.com/media/prints/572689/stls/4581551_c2dd1e18-28a2-41bf-b6e6-85b05d4153d8/right-gantry.stl">printables</a></td>
      <td>1</td>
      <td><a href="#right-gantry">More info</a></td>
    </tr>
    <tr>
      <td>Right Gantry Bottom</td>
      <td class="no-wrap"><a target="_blank" href="https://github.com/MSzturc/t100/blob/main/STL/Gantry/Right%20Gantry%20Bottom.stl">github</a> / <a href="https://files.printables.com/media/prints/572689/stls/4581550_449599ad-afa7-4b63-ab2b-89604bf1e875/right-gantry-bottom.stl">printables</a></td>
      <td>1</td>
      <td><a href="#right-gantry-bottom">More info</a></td>
    </tr>
  </tbody>
</table>

### Purchased Parts
<table class="table table-sm no-margin">
  <thead>
    <tr>
      <th scope="col">Item</th>
      <th scope="col">Qty</th>
      <th scope="col">Notes</th>
    </tr>
  </thead>
  <tbody>
    <tr>
      <td>m3 heat inserts</td>
      <td>12</td>
      <td></td>
    </tr>
    <tr>
      <td>m3x12 screw</td>
      <td>8</td>
      <td></td>
    </tr>
    <tr>
      <td>m5x30 screw</td>
      <td>2</td>
      <td></td>
    </tr>
    <tr>
      <td>m5x40 screw</td>
      <td>2</td>
      <td></td>
    </tr>
    <tr>
      <td>m5 washer</td>
      <td>8</td>
      <td>Exactly 1mm thick each</td>
    </tr>
    <tr>
      <td>Rod</td>
      <td>2</td>
      <td>Quality matters</td>
    </tr>
    <tr>
      <td>F695 bearing</td>
      <td>8</td>
      <td></td>
    </tr>
    <tr>
      <td>Drylin</td>
      <td>2</td>
      <td>Recommend brand name</td>
    </tr>
  </tbody>
</table>

### Details

#### Left Gantry
  
  
##### Print
<table class="table table-striped table-hover no-margin">
  <tbody class="table-group-divider">
    <tr>
      <th scope="row" class="no-wrap">Quantity</th>
      <td> </td>
      <td>1</td>
    </tr>
    <tr>
      <th scope="row" class="no-wrap">Filament Length</th>
      <td> </td>
      <td>12.2m</td>
    </tr>
    <tr>
      <th scope="row" class="no-wrap">Filament Weight</th>
      <td> </td>
      <td>36.4g</td>
    </tr>
    <tr>
      <th scope="row" class="no-wrap">Supports?</th>
      <td> </td>
      <td>No</td>
    </tr>
  </tbody>
</table>

##### Purchase
<table class="table table-striped table-hover no-margin">
  <thead>
    <tr>
      <th scope="col">Item</th>
      <th scope="col">Qty</th>
      <th scope="col">Note</th>
    </tr>
  </thead>
  <tbody>
    <tr>
      <td>m3 heat inserts</td>
      <td>6</td>
      <td></td>
    </tr>
    <tr>
      <td>m5x30 screw</td>
      <td>1</td>
      <td></td>
    </tr>
    <tr>
      <td>m5x40 screw</td>
      <td>1</td>
      <td></td>
    </tr>
    <tr>
      <td>m5 washer</td>
      <td>4</td>
      <td>Exactly 1mm thick</td>
    </tr>
  </tbody>
</table>

#### Left Gantry Bottom
  
  
##### Print
<table class="table table-striped table-hover no-margin">
  <tbody class="table-group-divider">
    <tr>
      <th scope="row" class="no-wrap">Quantity</th>
      <td> </td>
      <td>1</td>
    </tr>
    <tr>
      <th scope="row" class="no-wrap">Filament Length</th>
      <td> </td>
      <td>3m</td>
    </tr>
    <tr>
      <th scope="row" class="no-wrap">Filament Weight</th>
      <td> </td>
      <td>9g</td>
    </tr>
    <tr>
      <th scope="row" class="no-wrap">Supports?</th>
      <td> </td>
      <td>No</td>
    </tr>
  </tbody>
</table>

##### Purchase
<table class="table table-striped table-hover no-margin">
  <thead>
    <tr>
      <th scope="col">Item</th>
      <th scope="col">Qty</th>
      <th scope="col">Note</th>
    </tr>
  </thead>
  <tbody>
    <tr>
      <td>m3x12 screw</td>
      <td>4</td>
      <td></td>
    </tr>
    <tr>
      <td>Drylin linear bearing</td>
      <td>1</td>
      <td></td>
    </tr>
  </tbody>
</table>

#### Right Gantry
  
  
##### Print
<table class="table table-striped table-hover no-margin">
  <tbody class="table-group-divider">
    <tr>
      <th scope="row" class="no-wrap">Quantity</th>
      <td> </td>
      <td>1</td>
    </tr>
    <tr>
      <th scope="row" class="no-wrap">Filament Length</th>
      <td> </td>
      <td>12.2m</td>
    </tr>
    <tr>
      <th scope="row" class="no-wrap">Filament Weight</th>
      <td> </td>
      <td>36.4g</td>
    </tr>
    <tr>
      <th scope="row" class="no-wrap">Supports?</th>
      <td> </td>
      <td>No</td>
    </tr>
  </tbody>
</table>

##### Purchase
<table class="table table-striped table-hover no-margin">
  <thead>
    <tr>
      <th scope="col">Item</th>
      <th scope="col">Qty</th>
      <th scope="col">Note</th>
    </tr>
  </thead>
  <tbody>
    <tr>
      <td>m3 heat inserts</td>
      <td>6</td>
      <td></td>
    </tr>
    <tr>
      <td>m5x30 screw</td>
      <td>1</td>
      <td></td>
    </tr>
    <tr>
      <td>m5x40 screw</td>
      <td>1</td>
      <td></td>
    </tr>
    <tr>
      <td>m5 washer</td>
      <td>4</td>
      <td>Exactly 1mm thick</td>
    </tr>
  </tbody>
</table>

#### Right Gantry Bottom
  
  
##### Print
<table class="table table-striped table-hover no-margin">
  <tbody class="table-group-divider">
    <tr>
      <th scope="row" class="no-wrap">Quantity</th>
      <td> </td>
      <td>1</td>
    </tr>
    <tr>
      <th scope="row" class="no-wrap">Filament Length</th>
      <td> </td>
      <td>3m</td>
    </tr>
    <tr>
      <th scope="row" class="no-wrap">Filament Weight</th>
      <td> </td>
      <td>9g</td>
    </tr>
    <tr>
      <th scope="row" class="no-wrap">Supports?</th>
      <td> </td>
      <td>No</td>
    </tr>
  </tbody>
</table>

##### Purchase
<table class="table table-striped table-hover no-margin">
  <thead>
    <tr>
      <th scope="col">Item</th>
      <th scope="col">Qty</th>
      <th scope="col">Note</th>
    </tr>
  </thead>
  <tbody>
    <tr>
      <td>m3x12 screw</td>
      <td>4</td>
      <td></td>
    </tr>
    <tr>
      <td>Drylin linear bearing</td>
      <td>1</td>
      <td></td>
    </tr>
  </tbody>
</table>

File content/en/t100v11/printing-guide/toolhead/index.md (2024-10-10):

---
title: "Toolhead"
ogTitle: "Toolhead - THE 100 Print Guide"
description: "How to print THE 100's v1.1 toolhead, as well as what hardware you need to purchase to build it."
lead: ""
date: 2023-06-22T14:41:39+01:00
draft: false
images: []
type: docs
menu:
  t100v11:
    parent: "printing-guide-the100"
weight: 100
toc: true
doc: t100v11
images: 
  - images/tfd_toolhead_preview.png
---
# Toolhead
There are five total parts you need to print for the toolhead. Three are the same for all hotends and two vary depending on if you're using the Rapido UHF or CHC Pro hotend. 

<div class="row bd">
  <div class="col">
      

  </div>
  <div class="col">
    <ul class="list-group">
      <li class="list-group-item d-flex justify-content-between align-items-center">
        <div class="text fw-bold">Printed parts</div>
        <div class="text">5</div>
      </li>
    </ul>
    <br>
    <ul class="list-group">
      <li class="list-group-item d-flex justify-content-between align-items-center">
        <div class="text fw-bold">Purchased parts</div>
        <div class="text">40</div>
      </li>
    </ul>   
    <br>
    <ul class="list-group">
      <li class="list-group-item d-flex justify-content-between align-items-center">
        <div class="text fw-bold">Filament</div>
        <div class="text">43.2m | 128.6g</div>
      </li>
    </ul>   
    <br>
    <ul class="list-group">
      <li class="list-group-item d-flex justify-content-between align-items-center">
        <div class="text fw-bold">Print time</div>
        <div class="text">9h 13m</div>
      </li>
    </ul>   
  </div>
</div>

## Printed parts

### All Hotends
These parts are required regardless of which hotend you're using. 
<table class="table table-sm">
  <thead>
    <tr>
      <th scope="col">File Name</th>
      <th scope="col">STL</th>
      <th scope="col">Qty</th>
      <th scope="col">Notes</th>
    </tr>
  </thead>
  <tbody>
    <tr>
      <td>Connector Plate</td>
      <td><a href="https://github.com/MSzturc/t100/blob/main/STL/Toolhead/Connector%20Plate.stl" target="_blank">github</a> / <a href="https://files.printables.com/media/prints/572689/stls/4581540_86c6c691-8518-4868-aa2c-6b6cbf8d862b/connector-plate.stl">printables</a></td>
      <td>1</td>
      <td><a href="#connector-plate">More info</a></td>
    </tr>
    <tr>
      <td>Rod Cradle</td>
      <td><a href="https://github.com/MSzturc/t100/blob/main/STL/Toolhead/Rod-Cradle.stl" target="_blank">github</a> / <a href="https://files.printables.com/media/prints/572689/stls/4581539_80e2a55d-72a0-40fe-b1b5-6b485eb09bdf/rod-cradle.stl">printables</a></td>
      <td>1</td>
      <td><a href="#rod-cradle">More info</a></td>
    </tr>
  </tbody>
</table>

### CHC Pro Only
Print these if you're using the CHC Pro as your hotend. 
<table class="table table-sm">
  <thead>
    <tr>
      <th scope="col">File Name</th>
      <th scope="col">STL</th>
      <th scope="col">Qty</th>
      <th scope="col">Notes</th>
    </tr>
  </thead>
  <tbody>
    <tr>
      <td>CHC Pro Mount</td>
      <td><a href="https://github.com/MSzturc/t100/blob/main/STL/Toolhead/CHC%20Pro/CHC%20Pro%20Mount.stl" target="_blank">github</a> / <a href="">printables</a></td>
      <td>1</td>
      <td><a href="#chc-pro-mount">More info</a></td>
    </tr>
    <tr>
      <td>CHC Pro Clamp</td>
      <td><a href="https://github.com/MSzturc/t100/blob/main/STL/Toolhead/CHC%20Pro/CHC%20Pro%20Clamp.stl" target="_blank">github</a> / <a href="">printables</a></td>
      <td>1</td>
      <td><a href="#chc-pro-clamp">More info</a></td>
    </tr>
    <tr>
      <td>CHC Pro Fanduct</td>
      <td><a href="https://github.com/MSzturc/t100/blob/main/STL/Toolhead/CHC%20Pro/CHC%20Fanduct.stl" target="_blank">github</a> / <a href="">printables</a></td>
      <td>1</td>
      <td><a href="#chc-pro-fanduct">More info</a></td>
    </tr>
  </tbody>
</table>

### Rapido UHF Only
Print these if you're using the Rapido UHF as your hotend. 
<table class="table table-sm">
  <thead>
    <tr>
      <th scope="col">File Name</th>
      <th scope="col">STL</th>
      <th scope="col">Qty</th>
      <th scope="col">Notes</th>
    </tr>
  </thead>
  <tbody>
    <tr>
      <td>Rapido UHF Hotend Mount</td>
      <td><a href="https://github.com/MSzturc/t100/blob/main/STL/Toolhead/Rapido%20UHF/Hotend%20Mount.stl" target="_blank">github</a> / <a href="https://files.printables.com/media/prints/572689/stls/4581545_ed41faf4-5ea1-4cf9-acd4-890f96e3aae0/rapido-uhf-hotend-mount.stl">printables</a></td>
      <td>1</td>
      <td><a href="#rapido-uhf-hotend-mount">More info</a></td>
    </tr>
        <tr>
      <td>Rapido UHF Hotend Clamp</td>
      <td><a href="https://github.com/MSzturc/t100/blob/main/STL/Toolhead/Rapido%20UHF/Hotend%20Clamp.stl" target="_blank">github</a> / <a href="https://files.printables.com/media/prints/572689/stls/4581546_52f53683-e976-423d-bee0-2b05dd87a355/rapido-uhf-hotend-clamp.stl">printables</a></td>
      <td>1</td>
      <td><a href="#rapido-uhf-hotend-clamp">More info</a></td>
    </tr>
    <tr>
      <td>Rapido UHF Fan Duct</td>
      <td><a href="https://github.com/MSzturc/t100/blob/main/STL/Toolhead/Rapido%20UHF/Fan%20Duct.stl" target="_blank">github</a> / <a href="https://files.printables.com/media/prints/572689/stls/4581544_51661fc1-2705-4c38-aed4-1e143fcf5ddd/rapido-uhf-fan-duct.stl">printables</a></td>
      <td>1</td>
      <td><a href="#rapido-uhf-fan-duct">More info</a></td>
    </tr>
  </tbody>
</table>

## Purchased Parts
<table class="table table-sm no-margin">
  <thead>
    <tr>
      <th scope="col">Item</th>
      <th scope="col"> </th>
      <th scope="col">Qty</th>
      <th scope="col"> </th>
      <th scope="col">Notes</th>
    </tr>
  </thead>
  <tbody>
    <tr>
      <td>m3 heat insert</td>
      <td></td>
      <td>18</td>
      <td></td>
      <td>4 of them go in the fans</td>
    </tr>
    <tr>
      <td>m3x6 screw</td>
      <td></td>
      <td>12</td>
      <td></td>
      <td></td>
    </tr>
    <tr>
      <td>m3x12 screw</td>
      <td></td>
      <td>2</td>
      <td></td>
      <td></td>
    </tr>
    <tr>
      <td>m3x35 screw</td>
      <td></td>
      <td>1</td>
      <td></td>
      <td>Optional for cable management. Replaces 1x m3x6 if used.</td>
    </tr>
    <tr>
      <td>Drylin</td>
      <td></td>
      <td>2</td>
      <td></td>
      <td></td>
    </tr>
    <tr>
      <td>Linear rod</td>
      <td></td>
      <td>2</td>
      <td></td>
      <td></td>
    </tr>
    <tr>
      <td class="no-wrap">5015 blower fan</td>
      <td></td>
      <td>2</td>
      <td></td>
      <td></td>
    </tr>
    <tr>
      <td>4010 axial fan</td>
      <td></td>
      <td>1</td>
      <td></td>
      <td></td>
    </tr>
    <tr>
      <td>Hot end</td>
      <td></td>
      <td>1</td>
      <td></td>
      <td>This is more than 1 physical piece but I'm counting it as 1 total object</td>
    </tr>
  </tbody>
</table>

## Details
#### Connector Plate
  
  
##### Print
<table class="table table-striped table-hover no-margin">
  <tbody class="table-group-divider">
    <tr>
      <th scope="row" class="no-wrap">Quantity</th>
      <td> </td>
      <td>1</td>
    </tr>
    <tr>
      <th scope="row" class="no-wrap">Filament Length</th>
      <td> </td>
      <td>1m</td>
    </tr>
    <tr>
      <th scope="row" class="no-wrap">Filament Weight</th>
      <td> </td>
      <td>2.9g</td>
    </tr>
    <tr>
      <th scope="row" class="no-wrap">Supports?</th>
      <td> </td>
      <td>No</td>
    </tr>
  </tbody>
</table>

##### Purchase
<table class="table table-striped table-hover no-margin">
  <thead>
    <tr>
      <th scope="col">Item</th>
      <th scope="col">Qty</th>
      <th scope="col">Note</th>
    </tr>
  </thead>
  <tbody>
    <tr>
      <td>m3x6 screw</td>
      <td>4</td>
      <td></td>
    </tr>
  </tbody>
</table>

#### Rod Cradle
  
  
##### Print
<table class="table table-striped table-hover no-margin">
  <tbody class="table-group-divider">
    <tr>
      <th scope="row" class="no-wrap">Quantity</th>
      <td> </td>
      <td>1</td>
    </tr>
    <tr>
      <th scope="row" class="no-wrap">Filament Length</th>
      <td> </td>
      <td>8.6m</td>
    </tr>
    <tr>
      <th scope="row" class="no-wrap">Filament Weight</th>
      <td> </td>
      <td>25.6g</td>
    </tr>
    <tr>
      <th scope="row" class="no-wrap">Supports?</th>
      <td> </td>
      <td>Yes - See notes</td>
    </tr>
    <tr>
      <th scope="row" class="no-wrap">Note</th>
      <td> </td>
      <td>I rarely struggle with bed adhesion but out of the entire printer, this is the only one that gave me trouble. It kept getting knocked off. I ended up having to use a brim and enable z-hop to prevent it. Make sure supports are only used on the one end and that you don't generate supports through the square holes in the middle where the belts will go in the future. Support under the "triangle" shape against the build plate is probably unnecessary but it's a very small amount and helps ensure that piece, which slides in to the fanhead, is nice and flat. </td>
    </tr>
  </tbody>
</table>

##### Purchase
<table class="table table-striped table-hover no-margin">
  <thead>
    <tr>
      <th scope="col">Item</th>
      <th scope="col">Qty</th>
      <th scope="col">Note</th>
    </tr>
  </thead>
  <tbody>
    <tr>
      <td>m3 heat insert</td>
      <td>8</td>
      <td></td>
    </tr>
    <tr>
      <td>Drylin</td>
      <td>2</td>
      <td></td>
    </tr>
    <tr>
      <td>Linear rods</td>
      <td>2</td>
      <td></td>
    </tr>
  </tbody>
</table>

#### CHC Pro Fanduct
  
  
##### Print
<table class="table table-striped table-hover no-margin">
  <tbody class="table-group-divider">
    <tr>
      <th scope="row" class="no-wrap">Quantity</th>
      <td> </td>
      <td>1</td>
    </tr>
    <tr>
      <th scope="row" class="no-wrap">Filament Length</th>
      <td> </td>
      <td>29.5m</td>
    </tr>
    <tr>
      <th scope="row" class="no-wrap">Filament Weight</th>
      <td> </td>
      <td>87.9g</td>
    </tr>
    <tr>
      <th scope="row" class="no-wrap">Supports?</th>
      <td> </td>
      <td>Yes</td>
    </tr>
    <tr>
      <th scope="row" class="no-wrap">Note</th>
      <td> </td>
      <td>This piece is printed upside down to limit the amount of supports that need generated while still maintaining the openings for the airways. </td>
    </tr>
  </tbody>
</table>

##### Purchase
<table class="table table-striped table-hover no-margin">
  <thead>
    <tr>
      <th scope="col">Item</th>
      <th scope="col">Qty</th>
      <th scope="col">Note</th>
    </tr>
  </thead>
  <tbody>
    <tr>
      <td>m3 heat insert</td>
      <td>8</td>
      <td>4 go in the fans themselves. FAQ: 2 on the top are used to attach an accelerometer during tuning and aren't part of the actual construction.</td>
    </tr>
    <tr>
      <td>m3x6</td>
      <td>6</td>
      <td></td>
    </tr>
    <tr>
      <td>m3x35</td>
      <td>1</td>
      <td>Optional. Used for cable management. Replaces 1x m3x6.</td>
    </tr>
    <tr>
      <td></td>
      <td></td>
      <td></td>
    </tr>
  </tbody>
</table>

#### CHC Pro Mount
  
  
##### Print
<table class="table table-striped table-hover no-margin">
  <tbody class="table-group-divider">
    <tr>
      <th scope="row" class="no-wrap">Quantity</th>
      <td> </td>
      <td>1</td>
    </tr>
    <tr>
      <th scope="row" class="no-wrap">Filament Length</th>
      <td> </td>
      <td>3.4m</td>
    </tr>
    <tr>
      <th scope="row" class="no-wrap">Filament Weight</th>
      <td> </td>
      <td>10.1g</td>
    </tr>
    <tr>
      <th scope="row" class="no-wrap">Supports?</th>
      <td> </td>
      <td>Yes</td>
    </tr>
    <tr>
      <th scope="row" class="no-wrap">Note</th>
      <td> </td>
      <td>You may be able to avoid supports if your printer is good at bridging. </td>
    </tr>
  </tbody>
</table>

##### Purchase
<table class="table table-striped table-hover no-margin">
  <thead>
    <tr>
      <th scope="col">Item</th>
      <th scope="col">Qty</th>
      <th scope="col">Note</th>
    </tr>
  </thead>
  <tbody>
    <tr>
      <td>m3 heat insert</td>
      <td>2</td>
      <td></td>
    </tr>
    <tr>
      <td>m3x6 screw</td>
      <td>2</td>
      <td></td>
    </tr>
  </tbody>
</table>

#### CHC Pro Clamp
  
  
##### Print
<table class="table table-striped table-hover no-margin">
  <tbody class="table-group-divider">
    <tr>
      <th scope="row" class="no-wrap">Quantity</th>
      <td> </td>
      <td>1</td>
    </tr>
    <tr>
      <th scope="row" class="no-wrap">Filament Length</th>
      <td> </td>
      <td>0.7m</td>
    </tr>
    <tr>
      <th scope="row" class="no-wrap">Filament Weight</th>
      <td> </td>
      <td>2.1g</td>
    </tr>
    <tr>
      <th scope="row" class="no-wrap">Supports?</th>
      <td> </td>
      <td>Yes - in countersunk screw holes touching the build plate.</td>
    </tr>
  </tbody>
</table>

##### Purchase
<table class="table table-striped table-hover no-margin">
  <thead>
    <tr>
      <th scope="col">Item</th>
      <th scope="col">Qty</th>
      <th scope="col">Note</th>
    </tr>
  </thead>
  <tbody>
    <tr>
      <td>m3x12 screw</td>
      <td>2</td>
      <td></td>
    </tr>
  </tbody>
</table>

#### Rapido UHF Fan Duct
Coming soon

#### Rapido UHF Hotend Mount
Coming soon

#### Rapido UHF Hotend Clamp
Coming soon

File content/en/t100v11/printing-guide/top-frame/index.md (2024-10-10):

---
title: "Top Frame"
ogTitle: "Top Frame - THE 100 Print Guide"
description: "How to print THE 100's v1.1 top frame, as well as what hardware you need to purchase to build it."
lead: ""
date: 2023-06-18T14:41:39+01:00
draft: false
images: []
type: docs
menu:
  t100v11:
    parent: "printing-guide-the100"
weight: 150
toc: true
doc: t100v11
images: 
  - images/tfd_top_frame_preview.png
---
# Top Frame
A number of parts in this section won't get installed until you make more progress on the printer build, but they ultimately make up the top frame.

<div class="row bd">
  <div class="col">
      

  </div>
  <div class="col">
    <ul class="list-group">
      <li class="list-group-item d-flex justify-content-between align-items-center">
        <div class="text fw-bold">Printed parts</div>
        <div class="text">24</div>
      </li>
    </ul>
    <br>
    <ul class="list-group">
      <li class="list-group-item d-flex justify-content-between align-items-center">
        <div class="text fw-bold">Purchased parts</div>
        <div class="text">186</div>
      </li>
    </ul>   
    <br>
    <ul class="list-group">
      <li class="list-group-item d-flex justify-content-between align-items-center">
        <div class="text fw-bold">Filament</div>
        <div class="text">484.6m | 1430.2g</div>
      </li>
    </ul>   
    <br>
    <ul class="list-group">
      <li class="list-group-item d-flex justify-content-between align-items-center">
        <div class="text fw-bold">Print time</div>
        <div class="text">72h 20m</div>
      </li>
    </ul>   
  </div>
</div>

### Printed Parts
<table class="table table-sm no-margin">
  <thead>
    <tr>
      <th scope="col">Part Name</th>
      <th scope="col">STL</th>
      <th scope="col">Qty</th>
      <th scope="col">Notes</th>
    </tr>
  </thead>
  <tbody>
    <tr>
      <td>Belt Fastener</td>
      <td class="no-wrap"><a target="_blank" href="https://github.com/MSzturc/t100/blob/main/STL/Top%20Frame/Belt%20Fastener.stl">github</a> / <a href="https://files.printables.com/media/prints/572689/stls/4581525_87e472ef-6a36-43a6-9751-2e740efa957c/belt-fastener.stl">printables</a></td>
      <td>2</td>
      <td><a href="#belt-fastener">More info</a></td>
    </tr>
    <tr>
      <td>Connector Back 1</td>
      <td class="no-wrap"><a target="_blank" href="https://github.com/MSzturc/t100/blob/main/STL/Top%20Frame/Connector%20Back%201.stl">github</a> / <a href="https://files.printables.com/media/prints/572689/stls/4581521_58ea394e-0e60-4c26-a20c-f840b4769e91/connector-back-1.stl">printables</a></td>
      <td>1</td>
      <td><a href="#connector-back-1">More info</a></td>
    </tr>
    <tr>
      <td>Connector Back 2</td>
      <td class="no-wrap"><a target="_blank" href="https://github.com/MSzturc/t100/blob/main/STL/Top%20Frame/Connector%20Back%202.stl">github</a> / <a href="https://files.printables.com/media/prints/572689/stls/4581526_5ead97cb-c136-4222-af1e-1338eaf93d38/connector-back-2.stl">printables</a></td>
      <td>1</td>
      <td><a href="#connector-back-2">More info</a></td>
    </tr>
    <tr>
      <td>Connector Top 1</td>
      <td class="no-wrap"><a target="_blank" href="https://github.com/MSzturc/t100/blob/main/STL/Top%20Frame/Connector%20Top%201.stl">github</a> / <a href="https://files.printables.com/media/prints/572689/stls/4581523_fc47f4d9-1e6a-4674-b428-31dbb98269a5/connector-top-1.stl">printables</a></td>
      <td>1</td>
      <td><a href="#connector-top-1">More info</a></td>
    </tr>
    <tr>
      <td>Connector Top 2</td>
      <td class="no-wrap"><a target="_blank" href="https://github.com/MSzturc/t100/blob/main/STL/Top%20Frame/Connector%20Top%202.stl">github</a> / <a href="https://files.printables.com/media/prints/572689/stls/4581522_48b7d7f4-428e-416c-845a-8c07ec453f0d/connector-top-2.stl">printables</a></td>
      <td>1</td>
      <td><a href="#connector-top-2">More info</a></td>
    </tr>
    <tr>
      <td>Connector Side 1</td>
      <td class="no-wrap"><a target="_blank" href="https://github.com/MSzturc/t100/blob/main/STL/Top%20Frame/Connector%20Side%201.stl">github</a> / <a href="https://files.printables.com/media/prints/572689/stls/4581528_fe45c077-96dc-4319-a27a-93bbb7a6b970/connector-side-1.stl">printables</a></td>
      <td>4</td>
      <td><a href="#connector-side-1">More info</a></td>
    </tr>
    <tr>
      <td>Connector Side 2</td>
      <td class="no-wrap"><a target="_blank" href="https://github.com/MSzturc/t100/blob/main/STL/Top%20Frame/Connector%20Side%202.stl">github</a> / <a href="https://files.printables.com/media/prints/572689/stls/4581524_dd4b2992-6b76-43a2-be93-310f72eac41b/connector-side-2.stl">printables</a></td>
      <td>4</td>
      <td><a href="#connector-side-2">More info</a></td>
    </tr>
    <tr>
      <td>Rod Holder</td>
      <td class="no-wrap"><a target="_blank" href="https://github.com/MSzturc/t100/blob/main/STL/Top%20Frame/Rod%20Holder.stl">github</a> / <a href="https://files.printables.com/media/prints/572689/stls/4581529_092e02c4-49e1-44f1-a37d-18ee14bb61f9/rod-holder.stl">printables</a></td>
      <td>4</td>
      <td><a href="#rod-holder">More info</a></td>
    </tr>
    <tr>
      <td>Connector Z Left</td>
      <td class="no-wrap"><a target="_blank" href="https://github.com/MSzturc/t100/blob/main/STL/Top%20Frame/Connector%20Z%20Left.stl">github</a> / <a href="https://files.printables.com/media/prints/572689/stls/4581527_9c2a4baf-fbb4-4ba9-8ce3-d89dd9b1dbe0/connector-z-left.stl">printables</a></td>
      <td>1</td>
      <td><a href="#connector-z-leftright">More info</a></td>
    </tr>
    <tr>
      <td>Connector Z Right</td>
      <td class="no-wrap"><a target="_blank" href="https://github.com/MSzturc/t100/blob/main/STL/Top%20Frame/Connector%20Z%20Right.stl">github</a> / <a href="https://files.printables.com/media/prints/572689/stls/4581530_3b08857d-95f8-452c-8335-98f9c89fac01/connector-z-right.stl">printables</a></td>
      <td>1</td>
      <td><a href="#connector-z">More info</a></td>
    </tr>
    <tr>
      <td>Back-Left</td>
      <td class="no-wrap"><a target="_blank" href="https://github.com/MSzturc/t100/blob/main/STL/Top%20Frame/Back-Left.stl">github</a> / <a href="https://files.printables.com/media/prints/572689/stls/4581520_e9d51127-2714-4f46-b235-6020a2bf3863/back-left.stl">printables</a></td>
      <td>1</td>
      <td><a href="#back-left">More info</a></td>
    </tr>
    <tr>
      <td>Back-Right</td>
      <td class="no-wrap"><a target="_blank" href="https://github.com/MSzturc/t100/blob/main/STL/Top%20Frame/Back-Right.stl">github</a> / <a href="https://files.printables.com/media/prints/572689/stls/4581519_d103da9f-32e1-46c1-a790-b68a5a1b9ffb/back-right.stl">printables</a></td>
      <td>1</td>
      <td><a href="#back-right">More info</a></td>
    </tr>
    <tr>
      <td>Front-Left</td>
      <td class="no-wrap"><a target="_blank" href="https://github.com/MSzturc/t100/blob/main/STL/Top%20Frame/Front-Left.stl">github</a> / <a href="https://files.printables.com/media/prints/572689/stls/4581531_806e410e-28e8-4f55-8313-58586de8e733/front-left.stl">printables</a></td>
      <td>1</td>
      <td><a href="#front-left">More info</a></td>
    </tr>
    <tr>
      <td>Front-Right</td>
      <td class="no-wrap"><a target="_blank" href="https://github.com/MSzturc/t100/blob/main/STL/Top%20Frame/Front-Right.stl">github</a> / <a href="https://files.printables.com/media/prints/572689/stls/4581532_6a7080f7-c7c6-4703-8c3c-4d11c72910fa/front-right.stl">printables</a></td>
      <td>1</td>
      <td><a href="#front-right">More info</a></td>
    </tr>
  </tbody>
</table>

### Purchased Parts
<table class="table table-sm no-margin">
  <thead>
    <tr>
      <th scope="col">Item</th>
      <th scope="col">Qty</th>
      <th scope="col">Notes</th>
    </tr>
  </thead>
  <tbody>
    <tr>
      <td>m3 heat insert</td>
      <td>84</td>
      <td></td>
    </tr>
    <tr>
      <td>m3x10 screw</td>
      <td>8</td>
      <td></td>
    </tr>
    <tr>
      <td>m3x12 screw</td>
      <td>56</td>
      <td></td>
    </tr>
    <tr>
      <td>m3x16 screw</td>
      <td>4</td>
      <td></td>
    </tr>
    <tr>
      <td>m3x25 screw</td>
      <td>8</td>
      <td></td>
    </tr>
    <tr>
      <td>m3x35 screw</td>
      <td>10</td>
      <td></td>
    </tr>
    <tr>
      <td>m5x30 screw</td>
      <td>2</td>
      <td></td>
    </tr>
    <tr>
      <td>m5 washer</td>
      <td>6</td>
      <td></td>
    </tr>
    <tr>
      <td>F695 bearing</td>
      <td>8</td>
      <td></td>
    </tr>
  </tbody>
</table>

### Details

#### Belt Fastener 
  
  
##### Print
<table class="table table-striped table-hover no-margin">
  <tbody class="table-group-divider">
    <tr>
      <th scope="row" class="no-wrap">Quantity</th>
      <td> </td>
      <td>2</td>
    </tr>
    <tr>
      <th scope="row" class="no-wrap">Print Time</th>
      <td> </td>
      <td>36m</td>
    </tr>
    <tr>
      <th scope="row" class="no-wrap">Filament Length</th>
      <td> </td>
      <td>2.7m</td>
    </tr>
    <tr>
      <th scope="row" class="no-wrap">Filament Weight</th>
      <td> </td>
      <td>8.2g</td>
    </tr>
    <tr>
      <th scope="row" class="no-wrap">Supports?</th>
      <td> </td>
      <td>Yes - you may be able to get by without supports if your printer is good at bridging.</td>
    </tr>
  </tbody>
</table>

##### Purchase
<table class="table table-striped table-hover no-margin">
  <thead>
    <tr>
      <th scope="col">Item</th>
      <th scope="col">Qty</th>
      <th scope="col">Note</th>
    </tr>
  </thead>
  <tbody>
    <tr>
      <td>m3 nut</td>
      <td>1</td>
      <td>Insert before the bearing stack</td>
    </tr>
    <tr>
      <td>m5x30 screw</td>
      <td>1</td>
      <td></td>
    </tr>
    <tr>
      <td>F695 bearing</td>
      <td>4</td>
      <td></td>
    </tr>
    <tr>
      <td>m5 washer</td>
      <td>3</td>
      <td></td>
    </tr>
  </tbody>
</table>

#### Connector Back 1
  
  
##### Print
<table class="table table-striped table-hover no-margin">
  <tbody class="table-group-divider">
    <tr>
      <th scope="row" class="no-wrap">Quantity</th>
      <td> </td>
      <td>1</td>
    </tr>
    <tr>
      <th scope="row" class="no-wrap">Filament Length</th>
      <td> </td>
      <td>4.7m</td>
    </tr>
    <tr>
      <th scope="row" class="no-wrap">Filament Weight</th>
      <td> </td>
      <td>14.1g</td>
    </tr>
    <tr>
      <th scope="row" class="no-wrap">Supports?</th>
      <td> </td>
      <td>No</td>
    </tr>
  </tbody>
</table>

##### Purchase
<table class="table table-striped table-hover no-margin">
  <thead>
    <tr>
      <th scope="col">Item</th>
      <th scope="col">Qty</th>
      <th scope="col">Note</th>
    </tr>
  </thead>
  <tbody>
    <tr>
      <td>m3x12 screw</td>
      <td>4</td>
      <td></td>
    </tr>
  </tbody>
</table>

#### Connector Back 2
  
  
##### Print
<table class="table table-striped table-hover no-margin">
  <tbody class="table-group-divider">
    <tr>
      <th scope="row" class="no-wrap">Quantity</th>
      <td> </td>
      <td>1</td>
    </tr>
    <tr>
      <th scope="row" class="no-wrap">Filament Length</th>
      <td> </td>
      <td>4.2m</td>
    </tr>
    <tr>
      <th scope="row" class="no-wrap">Filament Weight</th>
      <td> </td>
      <td>12.6g</td>
    </tr>
    <tr>
      <th scope="row" class="no-wrap">Supports?</th>
      <td> </td>
      <td>No</td>
    </tr>
  </tbody>
</table>

##### Purchase
<table class="table table-striped table-hover no-margin">
  <thead>
    <tr>
      <th scope="col">Item</th>
      <th scope="col">Qty</th>
      <th scope="col">Note</th>
    </tr>
  </thead>
  <tbody>
    <tr>
      <td>m3x12 screw</td>
      <td>4</td>
      <td></td>
    </tr>
  </tbody>
</table>

#### Connector Top 1
  
  
##### Print
<table class="table table-striped table-hover no-margin">
  <tbody class="table-group-divider">
    <tr>
      <th scope="row" class="no-wrap">Quantity</th>
      <td> </td>
      <td>1</td>
    </tr>
    <tr>
      <th scope="row" class="no-wrap">Filament Length</th>
      <td> </td>
      <td>9.1m</td>
    </tr>
    <tr>
      <th scope="row" class="no-wrap">Filament Weight</th>
      <td> </td>
      <td>27.2g</td>
    </tr>
    <tr>
      <th scope="row" class="no-wrap">Supports?</th>
      <td> </td>
      <td>No</td>
    </tr>
    <tr>
      <th scope="row" class="no-wrap">Notes</th>
      <td> </td>
      <td>Uses screws that go all the way through in to nuts rather than heat inserts like the rest of the top frame connectors.</td>
    </tr>
  </tbody>
</table>

##### Purchase
<table class="table table-striped table-hover no-margin">
  <thead>
    <tr>
      <th scope="col">Item</th>
      <th scope="col">Qty</th>
      <th scope="col">Note</th>
    </tr>
  </thead>
  <tbody>
    <tr>
      <td>m3x25 screw</td>
      <td>8</td>
      <td>m3x30 will also work but sticks out slightly</td>
    </tr>
  </tbody>
</table>

#### Connector Top 2
  
  
##### Print
<table class="table table-striped table-hover no-margin">
  <tbody class="table-group-divider">
    <tr>
      <th scope="row" class="no-wrap">Quantity</th>
      <td> </td>
      <td>1</td>
    </tr>
    <tr>
      <th scope="row" class="no-wrap">Filament Length</th>
      <td> </td>
      <td>9.1m</td>
    </tr>
    <tr>
      <th scope="row" class="no-wrap">Filament Weight</th>
      <td> </td>
      <td>27.2g</td>
    </tr>
    <tr>
      <th scope="row" class="no-wrap">Supports?</th>
      <td> </td>
      <td>No</td>
    </tr>
    <tr>
      <th scope="row" class="no-wrap">Notes</th>
      <td> </td>
      <td>Uses inset nuts rather than heat inserts like the other top frame connectors.</td>
    </tr>
  </tbody>
</table>

##### Purchase
<table class="table table-striped table-hover no-margin">
  <thead>
    <tr>
      <th scope="col">Item</th>
      <th scope="col">Qty</th>
      <th scope="col">Note</th>
    </tr>
  </thead>
  <tbody>
    <tr>
      <td>m3 nut</td>
      <td>8</td>
      <td></td>
    </tr>
  </tbody>
</table>

#### Connector Side 1
  
  
##### Print
<table class="table table-striped table-hover no-margin">
  <tbody class="table-group-divider">
    <tr>
      <th scope="row" class="no-wrap">Quantity</th>
      <td> </td>
      <td>4</td>
    </tr>
    <tr>
      <th scope="row" class="no-wrap">Filament Length</th>
      <td> </td>
      <td>6.7m</td>
    </tr>
    <tr>
      <th scope="row" class="no-wrap">Filament Weight</th>
      <td> </td>
      <td>20.1g</td>
    </tr>
    <tr>
      <th scope="row" class="no-wrap">Supports?</th>
      <td> </td>
      <td>No</td>
    </tr>
  </tbody>
</table>

##### Purchase
<table class="table table-striped table-hover no-margin">
  <thead>
    <tr>
      <th scope="col">Item</th>
      <th scope="col">Qty</th>
      <th scope="col">Note</th>
    </tr>
  </thead>
  <tbody>
    <tr>
      <td>m3x12 screw</td>
      <td>8</td>
      <td></td>
    </tr>
  </tbody>
</table>

#### Connector Side 2     
  
  
##### Print
<table class="table table-striped table-hover no-margin">
  <tbody class="table-group-divider">
    <tr>
      <th scope="row" class="no-wrap">Quantity</th>
      <td> </td>
      <td>4</td>
    </tr>
    <tr>
      <th scope="row" class="no-wrap">Filament Length</th>
      <td> </td>
      <td>3.9m</td>
    </tr>
    <tr>
      <th scope="row" class="no-wrap">Filament Weight</th>
      <td> </td>
      <td>11.6g</td>
    </tr>
    <tr>
      <th scope="row" class="no-wrap">Supports?</th>
      <td> </td>
      <td>No</td>
    </tr>
  </tbody>
</table>

##### Purchase
<table class="table table-striped table-hover no-margin">
  <thead>
    <tr>
      <th scope="col">Item</th>
      <th scope="col">Qty</th>
      <th scope="col">Note</th>
    </tr>
  </thead>
  <tbody>
    <tr>
      <td>m3x12 screw</td>
      <td>4</td>
      <td></td>
    </tr>
  </tbody>
</table>

#### Rod Holder
  
  
##### Print
<table class="table table-striped table-hover no-margin">
  <tbody class="table-group-divider">
    <tr>
      <th scope="row" class="no-wrap">Quantity</th>
      <td> </td>
      <td>4</td>
    </tr>
    <tr>
      <th scope="row" class="no-wrap">Filament Length</th>
      <td> </td>
      <td>1.9m</td>
    </tr>
    <tr>
      <th scope="row" class="no-wrap">Filament Weight</th>
      <td> </td>
      <td>5.6g</td>
    </tr>
    <tr>
      <th scope="row" class="no-wrap">Supports?</th>
      <td> </td>
      <td>Yes - in the recessed screw holes touching the build plate</td>
    </tr>
  </tbody>
</table>

##### Purchase
<table class="table table-striped table-hover no-margin">
  <thead>
    <tr>
      <th scope="col">Item</th>
      <th scope="col">Qty</th>
      <th scope="col">Note</th>
    </tr>
  </thead>
  <tbody>
    <tr>
      <td>m3x35 screw</td>
      <td>2</td>
      <td></td>
    </tr>
  </tbody>
</table>  

#### Connector Z (Left/Right)
  
  
##### Print
<table class="table table-striped table-hover no-margin">
  <tbody class="table-group-divider">
    <tr>
      <th scope="row" class="no-wrap">Quantity</th>
      <td> </td>
      <td>2</td>
    </tr>
    <tr>
      <th scope="row" class="no-wrap">Filament Length</th>
      <td> </td>
      <td>5.4m</td>
    </tr>
    <tr>
      <th scope="row" class="no-wrap">Filament Weight</th>
      <td> </td>
      <td>16.2g</td>
    </tr>
    <tr>
      <th scope="row" class="no-wrap">Supports?</th>
      <td> </td>
      <td>Yes - in the recessed screw holes touching the build plate</td>
    </tr>
    <tr>
      <th scope="row">Note</th>
      <td> </td>
      <td>This is listed as 2 separate parts but it's actually the same part used twice.</td>
    </tr>
  </tbody>
</table>

##### Purchase
<table class="table table-striped table-hover no-margin">
  <thead>
    <tr>
      <th scope="col">Item</th>
      <th scope="col">Qty</th>
      <th scope="col">Note</th>
    </tr>
  </thead>
  <tbody>
    <tr>
      <td>m3x16 screw</td>
      <td>4</td>
      <td>m3x20 will also work</td>
    </tr>
  </tbody>
</table>

#### Back-Left
  
  
##### Print
<table class="table table-striped table-hover no-margin">
  <tbody class="table-group-divider">
    <tr>
      <th scope="row" class="no-wrap">Quantity</th>
      <td> </td>
      <td>1</td>
    </tr>
    <tr>
      <th scope="row" class="no-wrap">Filament Length</th>
      <td> </td>
      <td>104.2m</td>
    </tr>
    <tr>
      <th scope="row" class="no-wrap">Filament Weight</th>
      <td> </td>
      <td>310.7g</td>
    </tr>
    <tr>
      <th scope="row" class="no-wrap">Supports?</th>
      <td> </td>
      <td>Yes - You may be able to eliminate some supports if your printer can bridge over the square where the motor goes.</td>
    </tr>
    <tr>
      <th scope="row" class="no-wrap">Notes</th>
      <td> </td>
      <td>I recommend printing this piece with a brim to prevent warping. </td>
    </tr>
  </tbody>
</table>

##### Purchase
<table class="table table-striped table-hover no-margin">
  <thead>
    <tr>
      <th scope="col">Item</th>
      <th scope="col">Qty</th>
      <th scope="col">Note</th>
    </tr>
  </thead>
  <tbody>
    <tr>
      <td>m3 heat insert</td>
      <td>22</td>
      <td></td>
    </tr>
    <tr>
      <td>m3 nut</td>
      <td>2</td>
      <td>rod holder</td>
    </tr>
    <tr>
      <td>m3x10 screw</td>
      <td>4</td>
      <td>m3x12 should fit too but it depends on your motor</td>
    </tr>
  </tbody>
</table>

#### Back-Right
  
  
##### Print
<table class="table table-striped table-hover no-margin">
  <tbody class="table-group-divider">
    <tr>
      <th scope="row" class="no-wrap">Quantity</th>
      <td> </td>
      <td>1</td>
    </tr>
    <tr>
      <th scope="row" class="no-wrap">Filament Length</th>
      <td> </td>
      <td>104.7m</td>
    </tr>
    <tr>
      <th scope="row" class="no-wrap">Filament Weight</th>
      <td> </td>
      <td>312.4g</td>
    </tr>
    <tr>
      <th scope="row" class="no-wrap">Supports?</th>
      <td> </td>
      <td>Yes - You may be able to eliminate some supports if your printer can bridge over the square where the motor goes.</td>
    </tr>
    <tr>
      <th scope="row" class="no-wrap">Notes</th>
      <td> </td>
      <td>I recommend printing this piece with a brim to prevent warping. </td>
    </tr>
  </tbody>
</table>

##### Purchase
<table class="table table-striped table-hover no-margin">
  <thead>
    <tr>
      <th scope="col">Item</th>
      <th scope="col">Qty</th>
      <th scope="col">Note</th>
    </tr>
  </thead>
  <tbody>
    <tr>
      <td>m3 heat insert</td>
      <td>30</td>
      <td></td>
    </tr>
    <tr>
      <td>m3 nut</td>
      <td>2</td>
      <td>rod holder</td>
    </tr>
    <tr>
      <td>m3x10 screw</td>
      <td>4</td>
      <td>m3x12 should fit too but it depends on your motor</td>
    </tr>
  </tbody>
</table>

#### Front-Left
  
  
##### Print
<table class="table table-striped table-hover no-margin">
  <tbody class="table-group-divider">
    <tr>
      <th scope="row" class="no-wrap">Quantity</th>
      <td> </td>
      <td>1</td>
    </tr>
    <tr>
      <th scope="row" class="no-wrap">Filament Length</th>
      <td> </td>
      <td>91.2m</td>
    </tr>
    <tr>
      <th scope="row" class="no-wrap">Filament Weight</th>
      <td> </td>
      <td>272.1g</td>
    </tr>
    <tr>
      <th scope="row" class="no-wrap">Supports?</th>
      <td> </td>
      <td>Yes</td>
    </tr>
    <tr>
      <th scope="row" class="no-wrap">Notes</th>
      <td> </td>
      <td>I recommend printing this piece with a brim to prevent warping. </td>
    </tr>
  </tbody>
</table>

##### Purchase
<table class="table table-striped table-hover no-margin">
  <thead>
    <tr>
      <th scope="col">Item</th>
      <th scope="col">Qty</th>
      <th scope="col">Note</th>
    </tr>
  </thead>
  <tbody>
    <tr>
      <td>m3 heat insert</td>
      <td>16</td>
      <td></td>
    </tr>
    <tr>
      <td>m3 nut</td>
      <td>2</td>
      <td>rod holder</td>
    </tr>
    <tr>
      <td>m3x35 screw</td>
      <td>1</td>
      <td>Can go as low as m3x25, but doing m3x35 gives you maximum travel on the belt tensioner</td>
    </tr>
  </tbody>
</table>

#### Front-Right
  
  
##### Print
<table class="table table-striped table-hover no-margin">
  <tbody class="table-group-divider">
    <tr>
      <th scope="row" class="no-wrap">Quantity</th>
      <td> </td>
      <td>1</td>
    </tr>
    <tr>
      <th scope="row" class="no-wrap">Filament Length</th>
      <td> </td>
      <td>91.2m</td>
    </tr>
    <tr>
      <th scope="row" class="no-wrap">Filament Weight</th>
      <td> </td>
      <td>272.1g</td>
    </tr>
    <tr>
      <th scope="row" class="no-wrap">Supports?</th>
      <td> </td>
      <td>Yes</td>
    </tr>
    <tr>
      <th scope="row" class="no-wrap">Notes</th>
      <td> </td>
      <td>I recommend printing this piece with a brim to prevent warping. </td>
    </tr>
  </tbody>
</table>

##### Purchase
<table class="table table-striped table-hover no-margin">
  <thead>
    <tr>
      <th scope="col">Item</th>
      <th scope="col">Qty</th>
      <th scope="col">Note</th>
    </tr>
  </thead>
  <tbody>
    <tr>
      <td>m3 heat insert</td>
      <td>16</td>
      <td></td>
    </tr>
    <tr>
      <td>m3 nut</td>
      <td>2</td>
      <td>rod holder</td>
    </tr>
    <tr>
      <td>m3x35 screw</td>
      <td>1</td>
      <td>Can go as low as m3x25, but doing m3x35 gives you maximum travel on the belt tensioner</td>
    </tr>
  </tbody>
</table>

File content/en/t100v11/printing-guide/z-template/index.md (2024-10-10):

---
title: "Template"
ogTitle: "PART - THE 100 Print Guide"
description: "How to print THE 100's v1.1 PART, as well as what hardware you need to purchase to build it."
lead: ""
date: 2023-06-18T14:41:39+01:00
lastmod: 2023-06-21T00:41:39+01:00
draft: true
images: []
type: docs
menu:
  t100v11:
    parent: "printing-guide-the100"
weight: 999
toc: true
doc: t100v11
images: 
  - images/tfd_PART_preview.png
---
# Template
THE 100 template.

<div class="row bd">
  <div class="col">
      
  </div>
  <div class="col">
    <ul class="list-group">
      <li class="list-group-item d-flex justify-content-between align-items-center">
        <div class="text fw-bold">Printed parts</div>
        <div class="text">99</div>
      </li>
    </ul>
    <br>
    <ul class="list-group">
      <li class="list-group-item d-flex justify-content-between align-items-center">
        <div class="text">Purchased hardware</div>
        <div class="text">99</div>
      </li>
    </ul>   
    <br>
    <ul class="list-group">
      <li class="list-group-item d-flex justify-content-between align-items-center">
        <div class="text">Total filament</div>
        <div class="text">99m / 99g</div>
      </li>
    </ul>   
  </div>
</div>

### Printed parts
<table class="table table-sm">
  <thead>
    <tr>
      <th scope="col">GitHub</th>
      <th scope="col">Printables</th>
      <th scope="col">Qty</th>
      <th scope="col">Notes</th>
    </tr>
  </thead>
  <tbody>
    <tr>
      <td></td>
      <td><a href="">Part name</a></td>
      <td>1</td>
      <td><a href="#left-gantry">More info</a></td>
    </tr>
    <tr>
      <td></td>
      <td></td>
      <td></td>
      <td><a href="#">More info</a></td>
    </tr>
    <tr>
      <td></td>
      <td></td>
      <td>1</td>
      <td><a href="#">More info</a></td>
    </tr>
    <tr>
      <td></td>
      <td></td>
      <td>1</td>
      <td><a href="#">More info</a></td>
    </tr>
  </tbody>
</table>

### Purchased Parts
<table class="table table-sm no-margin">
  <thead>
    <tr>
      <th scope="col">Item</th>
      <th scope="col">Qty</th>
      <th scope="col">Notes</th>
    </tr>
  </thead>
  <tbody>
    <tr>
      <td></td>
      <td></td>
      <td></td>
    </tr>
    <tr>
      <td></td>
      <td></td>
      <td></td>
    </tr>
  </tbody>
</table>

### Details

#### PART
  
  
##### Print
<table class="table table-striped table-hover no-margin">
  <tbody class="table-group-divider">
    <tr>
      <th scope="row" class="no-wrap">Quantity</th>
      <td> </td>
      <td>1</td>
    </tr>
    <tr>
      <th scope="row" class="no-wrap">Filament Length</th>
      <td> </td>
      <td>0m</td>
    </tr>
    <tr>
      <th scope="row" class="no-wrap">Filament Weight</th>
      <td> </td>
      <td>0g</td>
    </tr>
    <tr>
      <th scope="row" class="no-wrap">Supports?</th>
      <td> </td>
      <td>No</td>
    </tr>
    <tr>
      <th scope="row" class="no-wrap">Supports?</th>
      <td> </td>
      <td>Note</td>
    </tr>
  </tbody>
</table>

##### Purchase
<table class="table table-striped table-hover no-margin">
  <thead>
    <tr>
      <th scope="col">Item</th>
      <th scope="col">Qty</th>
      <th scope="col">Note</th>
    </tr>
  </thead>
  <tbody>
    <tr>
      <td>Heat inserts</td>
      <td>0</td>
      <td></td>
    </tr>
    <tr>
      <td>m3x10mm screw</td>
      <td>2</td>
      <td>For going in to something</td>
    </tr>
  </tbody>
</table>

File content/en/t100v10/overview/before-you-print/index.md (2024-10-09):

---
title: "Before you print"
description: "What to know before you start printing THE 100 3d printer"
lead: ""
date: 2023-06-18T14:41:39+01:00
lastmod: 2023-06-21T00:41:39+01:00
draft: false
images: []
type: docs
menu:
  t100v10:
    parent: "overview-v10"
    identifier: "before-you-print-v10"
weight: 70
toc: true
doc: t100v10
aliases:
  - /t100/overview/before-you-print/
---
# Before you start printing

The printhead, frame, gantry, and more are all 3d printed parts. That's what makes this printer so awesome. But for obvious reasons there are still a number of items that need to be purchased. 

The official BOM is available <a href="https://docs.google.com/spreadsheets/d/1qVG3n-1HVcA7c-vKpUakU7fWirMONmqOiJRv8SHPkTo/edit#gid=0">here</a>. I suggest reviewing it and confirming you can get everything you need prior to starting to print the parts. 

Some of the more expensive parts or more commonly asked about parts are (in no particular order):

  * Ender 2 Pro heated bed (yes, Ender 2. Not 3)
  * SKR Pico mainboard
  * Banana Pi M2 Zero
  * ~3KG of filament

I was able to purchase everything I needed off AliExpress. In the future I will post links to the companies I used.

## STL Links
Each part contains a link to the STL on GitHub and the STL on Printables. In nearly every case the filenames are different, and in a few cases there are parts differences between the two. I have included the filenames in the links to help you understand how the parts align between the two sources. Make sure to read the part notes if you're confused about a particular part. 

## Warning

The current revision of this guide is based on THE 100 v1.0. The biggest issue with that is I never actually printed v1.0. I support Matt on Patreon and through that I had access to newer parts and I printed those instead. The printer I made is much closer to v1.1 than it is v1. That means my counts for screws and heat inserts will be slightly off because I don't have an actual machine to compare them to. It also means I don't have any tips/tricks that are specific to v1.0 because I didn't print it.

I will be updating this guide to reference v1.1 parts but at the moment they're a Patreon exclusive so I won't be distributing them.

## Print settings

I printed all parts with a 0.6 nozzle using the <a href="https://github.com/MSzturc/the100#print-settings">recomended print settings</a> which are:

  * 0.25 Layer height
  * 0.5 Line width
  * 3 Top layers
  * 3 Bottom layers
  * 3 Walls
  * Grid Infill Pattern
  * 25% Infill
    * Use 30% infill for the print bed to move the center of gravity to where it's needed

## Additional info and support

This project wouldn't exist without Matt so I wanted to provide a list of links back to him and his resources:

  * <a href="https://github.com/MSzturc/the100">GitHub</a>
  * <a href="https://discord.gg/fW7BcUErgZ">Discord</a>
    * You can find me on here as `TheForgetfulDev`. Please reach out if you notice any issues with this guide or if you have any questions about the build.
  * <a href="https://www.patreon.com/The100">Patreon</a>
  * <a href="https://www.youtube.com/playlist?list=PLM01o_dfwbDcKYB-9yV0vLs5k0CrHUv0W">YouTube</a>
  * <a href="https://hackaday.io/project/190348-the-100-the-fastest-3d-printer">hackaday</a>

Ok, <a href="/t100/1.0/printing-guide/toolhead/">let's get printing</a>!

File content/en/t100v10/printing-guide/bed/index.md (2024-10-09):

---
title: "Bed"
description: "Print THE 100 Bed title."
lead: ""
date: 2023-06-18T14:41:39+01:00
lastmod: 2023-06-21T00:41:39+01:00
draft: false
images: []
type: docs
menu:
  t100v10:
    parent: "printing-guide-the100"
weight: 350
toc: true
doc: t100v10
aliases:
  - /t100/printing-guide/bed/
---
# Bed
Everything you need to print for THE 100 bed.

As mentioned in <a href="/t100/overview/before-you-print/#print-settings">print settings</a>, these parts should be printed with 30% infill. 

## v1.0

### Parts List
<table class="table table-sm">
  <thead>
    <tr>
      <th scope="col">GitHub</th>
      <th scope="col">Printables</th>
      <th scope="col">Qty</th>
      <th scope="col">Notes</th>
    </tr>
  </thead>
  <tbody>
    <tr>
      <td><a href="https://github.com/MSzturc/t100/blob/main/STL/Bed/Center.stl">Center</a></td>
      <td><a href="https://files.printables.com/media/prints/430339/stls/3564416_e3f2e0b0-8d64-4022-89af-17159b7de61b/bed-center.stl">Bed-Center</a></td>
      <td>1</td>
      <td><a href="#center">More info</a></td>
    </tr>
    <tr>
      <td><a href="https://github.com/MSzturc/t100/blob/main/STL/Bed/Left.stl">Left</a></td>
      <td><a href="https://files.printables.com/media/prints/430339/stls/3564426_db9391c8-82f4-497a-851d-506891bc1b62/bed-right.stl">Bed-Right</a></td>
      <td>1</td>
      <td><a href="#left">More info</a></td>
    </tr>
    <tr>
      <td><a href="https://github.com/MSzturc/t100/blob/main/STL/Bed/Right.stl">Right</a></td>
      <td><a href="https://files.printables.com/media/prints/430339/stls/3564413_f90868f1-1f46-42cb-a85a-6df9317f094a/bed-left.stl">Bed-Left</a></td>
      <td>1</td>
      <td><a href="#right">More info</a></td>
    </tr>
  </tbody>
</table>

### More Info

#### Center

##### Printing details
  - Qty: 1
  - Filament (length/weight): 72m / 215g
  - Supports: No

##### Notes
A brim is recommended to help keep the bed from warping. 



#### Left

##### Printing details
  - Qty: 1
  - Filament (length/weight): 42m / 125g
  - Supports: Yes

##### Notes
A brim is recommended to help keep the bed from warping. Needs to be oriented at an angle to fit on a 225x225 bed like the Ender 3 (or be willing to override settings in your slicer to tell it to slice anyways). 



#### Right

##### Printing details
  - Qty: 1
  - Filament (length/weight): 42m / 125g
  - Supports: Yes

##### Notes
A brim is recommended to help keep the bed from warping. Needs to be oriented at an angle to fit on a 225x225 bed like the Ender 3 (or be willing to override settings in your slicer to tell it to slice anyways). 



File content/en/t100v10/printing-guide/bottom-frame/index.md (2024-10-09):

---
title: "Bottom Frame"
description: ""
lead: ""
date: 2023-06-18T14:41:39+01:00
lastmod: 2023-06-21T00:41:39+01:00
draft: false
images: []
type: docs
menu:
  t100v10:
    parent: "printing-guide-the100"
weight: 340
toc: true
doc: t100v10
aliases:
  - /t100/printing-guide/bottom-frame/
---
# Bottom Frame
## v1.0

### Parts List
These parts are required regardless of which hotend you're using. 
<table class="table table-sm">
  <thead>
    <tr>
      <th scope="col">GitHub</th>
      <th scope="col">Printables</th>
      <th scope="col">Qty</th>
      <th scope="col">Notes</th>
    </tr>
  </thead>
  <tbody>
    <tr>
      <td><a href="https://github.com/MSzturc/t100/blob/main/STL/Bottom%20Frame/Bottom%201.stl">Bottom 1</a></td>
      <td><a href="https://files.printables.com/media/prints/430339/stls/3564418_21f0869b-b5ae-4c2a-80cf-f1be2cf639b5/bottom-frame-back-left.stl">Bottom Frame Back Left</a></td>
      <td>1</td>
      <td><a href="#back-left">More info</a></td>
    </tr>
    <tr>
      <td><a href="https://github.com/MSzturc/t100/blob/main/STL/Bottom%20Frame/Bottom%202.stl">Bottom 2</a></td>
      <td><a href="https://files.printables.com/media/prints/430339/stls/3564421_adf6ab3d-a6b8-42ec-974a-da9ccf200aae/bottom-frame-back-right.stl">Bottom Frame Back Right</a></td>
      <td>1</td>
      <td><a href="#back-right">More info</a></td>
    </tr>
    <tr>
      <td><a href="https://github.com/MSzturc/t100/blob/main/STL/Bottom%20Frame/Bottom%203.stl">Bottom 3</a></td>
      <td><a href="https://files.printables.com/media/prints/430339/stls/3564428_418fdab3-c5c8-4d97-ac88-ef0fffa61c0d/bottom-frame-front-left.stl">Bottom Frame Front Left</a></td>
      <td>1</td>
      <td><a href="#front-left">More info</a></td>
    </tr>
    <tr>
      <td><a href="https://github.com/MSzturc/t100/blob/main/STL/Bottom%20Frame/Bottom%204.stl">Bottom 4</a></td>
      <td><a href="https://files.printables.com/media/prints/430339/stls/3564409_2ee0713c-c46e-4681-8bb1-50b12ee2195b/bottom-frame-front-right.stl">Bottom Frame Front Right</a></td>
      <td>1</td>
      <td><a href="#front-right">More info</a></td>
    </tr>
    <tr>
      <td><a href="https://github.com/MSzturc/t100/blob/main/STL/Bottom%20Frame/Connection%20Back.stl">Connection Back</a></td>
      <td><a href="https://files.printables.com/media/prints/430339/stls/3564420_a1449d3b-6783-44b8-82ad-53782753ae51/bottom-frame-connector-back.stl">Bottom Frame Connector Back</a></td>
      <td>1</td>
      <td><a href="#connector-back">More info</a></td>
    </tr>
    <tr>
      <td><a href="https://github.com/MSzturc/t100/blob/main/STL/Bottom%20Frame/Connection%20Front%201.stl">Connection Front 1</a></td>
      <td><a href="https://files.printables.com/media/prints/430339/stls/3564415_84477a66-25ea-4094-b21b-741d9e834e63/bottom-frame-connector-front-1.stl">Bottom Frame Connector Front 1</a></td>
      <td>1</td>
      <td><a href="#connector-front-1">More info</a></td>
    </tr>
    <tr>
      <td><a href="https://github.com/MSzturc/t100/blob/main/STL/Bottom%20Frame/Connection%20Front%202.stl">Connection Front 2</a></td>
      <td><a href="https://files.printables.com/media/prints/430339/stls/3564419_f0b60644-d1cf-48e0-866e-c45ae660c17f/bottom-frame-connector-front-2.stl">Bottom Frame Connector Front 2</a></td>
      <td>1</td>
      <td><a href="#connector-front-2">More info</a></td>
    </tr>
    <tr>
      <td><strike>Connection Left</strike></td>
      <td><a href="https://files.printables.com/media/prints/430339/stls/3564410_9e694d5d-cf28-4172-8b55-69274073c180/bottom-frame-connector-left-1.stl">Bottom Frame Connector Left 1</a></td>
      <td>1</td>
      <td><a href="#connector-left-1">More info</a></td>
    </tr>
    <tr>
      <td>See info</td>
      <td><a href="https://files.printables.com/media/prints/430339/stls/3564414_82e2226d-9537-4c4f-a1dc-31044f685f3f/bottom-frame-connector-left-2.stl">Bottom Frame Connector Left 2</a></td>
      <td>1</td>
      <td><a href="#connector-left-2">More info</a></td>
    </tr>
    <tr>
      <td><strike>Connection Right</strike></td>
      <td><a href="https://files.printables.com/media/prints/430339/stls/3564412_139d64d7-5bfd-4b9b-84b1-a57581b02cee/bottom-frame-connector-right-1.stl">Bottom Frame Connector Right 1</a></td>
      <td>1</td>
      <td><a href="#connector-right-1">More info</a></td>
    </tr>
    <tr>
      <td>See info</td>
      <td><a href="https://files.printables.com/media/prints/430339/stls/3564402_ab155e55-95cc-4285-8caf-35985d2e5be8/bottom-frame-connector-right-2.stl">Bottom Frame Connector Right 2</a></td>
      <td>1</td>
      <td><a href="#connector-right-2">More info</a></td>
    </tr>
    <tr>
      <td><a href="https://github.com/MSzturc/t100/blob/main/STL/Bottom%20Frame/Foot.stl">Foot</a></td>
      <td><a href="https://files.printables.com/media/prints/430339/stls/3564423_bfd498fa-dd66-4345-96a6-25d1be53fe75/bottom-foot-back-left.stl">Bottom Foot Back Left</a></td>
      <td>4</td>
      <td><a href="#foot">More info</a></td>
    </tr>
    <tr>
      <td>n/a</td>
      <td><a href="https://files.printables.com/media/prints/430339/stls/3564393_03d9394b-5c80-48cf-a571-ee4341b42e73/5mm-8mm-coupler.stl">5mm - 8mm Coupler</a></td>
      <td>2</td>
      <td><a href="#5mm---8mm-coupler">More info</a></td>
    </tr>
  </tbody>
</table>

### More Info

#### Back Left
##### Printing details
  - Qty: 1
  - Filament (length/weight): 37.4m / 111.5g
  - Supports: No


##### Notes
A brim is recommended to prevent warping.

#### Back Right
##### Printing details
  - Qty: 1
  - Filament (length/weight): 37.1m / 110.7g
  - Supports: No


##### Notes
A brim is recommended to prevent warping.

#### Front Left
##### Printing details
  - Qty: 1
  - Filament (length/weight): 50.9m / 151.9g
  - Supports: Yes - only needed for countersunk screw holes that are touching the build plate


##### Notes
A brim is recommended to prevent warping. 

#### Front Right
##### Printing details
  - Qty: 1
  - Filament (length/weight): 51.5m / 153.8g
  - Supports: Yes - only needed for countersunk screw holes that are touching the build plate


##### Notes
A brim is recommended to prevent warping.

#### Connector Back
##### Printing details
  - Qty: 1
  - Filament (length/weight): 5.5m / 16.5g
  - Supports: No


##### Notes
None

#### Connector Front 1
##### Printing details
  - Qty: 1
  - Filament (length/weight): 4.1m / 12.4g
  - Supports: No


##### Notes
None

#### Connector Front 2
##### Printing details
  - Qty: 1
  - Filament (length/weight): 4.2m / 12.4g
  - Supports: No


##### Notes
None

#### Connector Left 1
##### Printing details
  - Qty: 1
  - Filament (length/weight): 3m / 8.8g
  - Supports: No


##### Notes
The github version only contains `Connection Left` with no matching part for the other side, meaning it has nothing to attach to. You need to also get `Bottom Frame Connector Left 1` from Printables.  

#### Connector Left 2
##### Printing details
  - Qty: 1
  - Filament (length/weight): 2.9m / 8.7g
  - Supports: No


##### Notes
The github version doesn't have this part. You need to get it from Printables. 

#### Connector Right 1
##### Printing details
  - Qty: 1
  - Filament (length/weight): 2.9m / 8.7g
  - Supports: No


##### Notes
The github version only contains `Connection Right` with no matching part for the other side, meaning it has nothing to attach to. You need to also get `Bottom Frame Connector Right 1` from Printables.  

#### Connector Right 2
##### Printing details
  - Qty: 1
  - Filament (length/weight): 2.9m / 8.7g
  - Supports: No


##### Notes
The github version doesn't have this part. You need to get it from Printables. 

#### Foot
##### Printing details
  - Qty: 4
  - Filament (length/weight): 10.5m / 31.4g
  - Supports: No


##### Notes
Printables contains separate 4 stls for the 4 separate feet but they're all the same thing. Just print 1 of them 4 times. 

#### 5mm - 8mm Coupler
##### Printing details
  - Qty: 2
  - Filament (length/weight): 2.1m / 6.4g
  - Supports: No


##### Notes
This doesn't exist on GitHub but is a necessary part if you didn't purchase it. These allow you to connect the screw rod to the motor. I printed mine in petg but that's mainly because it was already loaded in my printer. I think PLA is perfectly fine for this part.

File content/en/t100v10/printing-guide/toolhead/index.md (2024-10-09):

---
title: "Toolhead"
description: ""
lead: ""
date: 2023-06-18T14:41:39+01:00
lastmod: 2023-06-21T00:41:39+01:00
draft: false
images: []
type: docs
menu:
  t100v10:
    parent: "printing-guide-the100"
weight: 300
toc: true
doc: t100v10
aliases:
  - /t100/printing-guide/toolhead/
---
# THE 100 Toolhead
Everything you need to print for THE 100 toolhead.

There are five total parts you need to print for the toolhead. Three are the same for all hotends and two vary depending on if you're using the CHC or CHC Pro hotend. 

## v1.0

### Parts List - All Hotends
These parts are required regardless of which hotend you're using. 
<table class="table table-sm">
  <thead>
    <tr>
      <th scope="col">GitHub</th>
      <th scope="col">Printables</th>
      <th scope="col">Qty</th>
      <th scope="col">Notes</th>
    </tr>
  </thead>
  <tbody>
    <tr>
      <td><a href="https://github.com/MSzturc/t100/blob/main/STL/Hotend/Connection%20Fanhead.stl">Connection Fanhead</a></td>
      <td><a href="https://files.printables.com/media/prints/430339/stls/3564396_25aa452a-3a7d-4a5a-b203-1c0284850b7d/adapter-plate.stl">Adapter Plate</a></td>
      <td>1</td>
      <td><a href="#adapter-plate">More info</a></td>
    </tr>
    <tr>
      <td><a href="https://github.com/MSzturc/t100/blob/main/STL/Hotend/Rod-Cradle.stl">Rod Cradle</a></td>
      <td><a href="https://files.printables.com/media/prints/430339/stls/3564389_4fe028b8-ebe9-4c5a-9efd-981826b06630/rod-carriage.stl">Rod Carriage</a></td>
      <td>1</td>
      <td><a href="#rod-carriage">More info</a></td>
    </tr>
    <tr>
      <td><a href="https://github.com/MSzturc/t100/blob/main/STL/Hotend/TD6%20Fanhead.stl">TD6 Fanhead</a></td>
      <td><a href="https://files.printables.com/media/prints/430339/stls/3564386_5ab1e0bd-4a8d-454e-baed-8f8e13749b73/fanhead.stl">Fanhead</a></td>
      <td>1</td>
      <td><a href="#fanhead">More info</a></td>
    </tr>
  </tbody>
</table>

### Parts List - CHC Pro Only
Print these if you're using the CHC Pro as your hotend. 
<table class="table table-sm">
  <thead>
    <tr>
      <th scope="col">GitHub</th>
      <th scope="col">Printables</th>
      <th scope="col">Qty</th>
      <th scope="col">Notes</th>
    </tr>
  </thead>
  <tbody>
    <tr>
      <td><a href="https://github.com/MSzturc/t100/blob/main/STL/Hotend/CHC%20Pro/TD6%20PRO%20Tool-Mount.stl">TD6 PRO Tool-Mount</a></td>
      <td><a href="https://files.printables.com/media/prints/430339/stls/3564397_6b45327a-8ad4-4698-b4a5-531f8660638e/chc-pro-mount.stl">CHC Pro Mount</a></td>
      <td>1</td>
      <td><a href="#chc-pro-mount">More info</a></td>
    </tr>
    <tr>
      <td><a href="https://github.com/MSzturc/t100/blob/main/STL/Hotend/CHC%20Pro/TD6%20Pro%20Front.stl">TD6 Pro Front</a></td>
      <td><a href="https://files.printables.com/media/prints/430339/stls/3564388_47d61a0b-f98a-4692-88e8-fd640e794ecf/chc-pro-mount-front.stl">CHC PRO Mount Front</a></td>
      <td>1</td>
      <td><a href="#chc-pro-mount-front">More info</a></td>
    </tr>
  </tbody>
</table>

### Parts List - CHC Only
Print these if you're using the CHC (not pro) as your hotend. 
<table class="table table-sm">
  <thead>
    <tr>
      <th scope="col">GitHub</th>
      <th scope="col">Printables</th>
      <th scope="col">Qty</th>
      <th scope="col">Notes</th>
    </tr>
  </thead>
  <tbody>
    <tr>
      <td><a href="https://github.com/MSzturc/t100/blob/main/STL/Hotend/CHC/TD6%20Tool-Mount.stl">TD6 Tool-Mount</a></td>
      <td><a href="https://files.printables.com/media/prints/430339/stls/3564401_f91ab511-ed0d-4e4b-ba4d-471b86d19df3/chc-mount.stl">CHC Mount</a></td>
      <td>1</td>
      <td><a href="#chc-mount">More info</a></td>
    </tr>
        <tr>
      <td><a href="https://github.com/MSzturc/t100/blob/main/STL/Hotend/CHC/TD6%20Front.stl">TD6 Front</a></td>
      <td><a href="https://files.printables.com/media/prints/430339/stls/3564401_f91ab511-ed0d-4e4b-ba4d-471b86d19df3/chc-mount.stl">CHC Mount Front</a></td>
      <td>1</td>
      <td><a href="#chc-mount-front">More info</a></td>
    </tr>
  </tbody>
</table>

### More Info

#### Adapter Plate

##### Printing details
  - Qty: 1
  - Filament (length/weight): 1m / 2.9g
  - Supports: No

  

##### Notes
None

#### Rod Carriage

##### Printing details
  - Qty: 1
  - Filament (length/weight): 8.6m / 25.7g
  - Supports: Yes

  

##### Notes
I rarely struggle with bed adhesion but out of the entire printer, this is the only one that gave me trouble. It kept getting knocked off. I ended up having to use a brim and enable z-hop to prevent it. Make sure supports are only used on the one end and that you don't generate supports through the square holes in the middle where the belts will go in the future.

#### Fanhead

##### Printing details
  - Qty: 1
  - Filament (length/weight): 20.7m / 61.6g
  - Supports: Yes

  

##### Notes
Only generate suports under the curved parts against the build plate. This piece is printed upside down to limit the amount of supports that need generated while still maintaining the openings for the airways. 

#### CHC Pro Mount

##### Printing details
  - Qty: 1
  - Filament (length/weight): 3.5m / 10.4g
  - Supports: Yes

  

##### Notes
None

#### CHC Pro Mount Front

##### Printing details
  - Qty: 1
  - Filament (length/weight): 0.69m / 2g
  - Supports: No

  

##### Notes
None

#### CHC Mount

##### Printing details
  - Qty: 1
  - Filament (length/weight): 3.5m / 10.4g
  - Supports: Yes

##### Notes
See CHC Pro Toolhead for print orientation

#### CHC Mount Front

##### Printing details
  - Qty: 1
  - Filament (length/weight): 0.66m / 1.9g
  - Supports: No

##### Notes
See CHC Pro Front for print orientation

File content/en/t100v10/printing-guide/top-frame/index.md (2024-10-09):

---
title: "Top Frame"
description: ""
lead: ""
date: 2023-06-18T14:41:39+01:00
lastmod: 2023-06-21T00:41:39+01:00
draft: false
images: []
type: docs
menu:
  t100v10:
    parent: "printing-guide-the100"
weight: 330
toc: true
doc: t100v10
aliases:
  - /t100/printing-guide/top-frame/
---
# Top Frame
Everything you need to print for THE 100 top frame.

## v1.0

### Parts List
These parts are required regardless of which hotend you're using. 
<table class="table table-sm">
  <thead>
    <tr>
      <th scope="col">GitHub</th>
      <th scope="col">Printables</th>
      <th scope="col">Qty</th>
      <th scope="col">Notes</th>
    </tr>
  </thead>
  <tbody>
    <tr>
      <td><a href="https://github.com/MSzturc/t100/blob/main/STL/Top%20Frame/BeltFastener.stl">BeltFastener</a></td>
      <td><a href="https://files.printables.com/media/prints/430339/stls/3564390_ddfa3de1-714e-44a9-b9f8-72145f202c47/belt-fastener.stl">Belt Fastener</a></td>
      <td>2</td>
      <td><a href="#belt-fastener">More info</a></td>
    </tr>
    <tr>
      <td><a href="https://github.com/MSzturc/t100/blob/main/STL/Top%20Frame/Connection%20Back%201.stl">Connection Back 1</a></td>
      <td><a href="https://files.printables.com/media/prints/430339/stls/3564411_7cf449ba-444e-43f2-b526-7b290b5dcee5/top-connector-back-1.stl">Top Connector Back 1</a></td>
      <td>1</td>
      <td><a href="#top-connector-back-1">More info</a></td>
    </tr>
    <tr>
      <td><a href="https://github.com/MSzturc/t100/blob/main/STL/Top%20Frame/Connection%20Back%202.stl">Connection Back 2</a></td>
      <td><a href="https://files.printables.com/media/prints/430339/stls/3564417_d1e46c84-f62e-468b-a5f7-c69d9b4f8ab5/top-connector-back-2.stl">Top Connector Back 2</a></td>
      <td>1</td>
      <td><a href="#top-connector-back-2">More info</a></td>
    </tr>
    <tr>
      <td><a href="https://github.com/MSzturc/t100/blob/main/STL/Top%20Frame/Connection%20Front%201.stl">Connection Front 1</a></td>
      <td><a href="https://files.printables.com/media/prints/430339/stls/3564399_dc9e1757-861b-4e85-8e95-2cce881eab23/top-connector-top-2.stl">Top Connector Top 1</a></td>
      <td>1</td>
      <td><a href="#top-connector-top-1">More info</a></td>
    </tr>
    <tr>
      <td><a href="https://github.com/MSzturc/t100/blob/main/STL/Top%20Frame/Connection%20Front%202.stl">Connection Front 2</a></td>
      <td><a href="https://files.printables.com/media/prints/430339/stls/3564399_dc9e1757-861b-4e85-8e95-2cce881eab23/top-connector-top-2.stl">Top Connector Top 2</a></td>
      <td>1</td>
      <td><a href="#top-connector-top-2">More info</a></td>
    </tr>
    <tr>
      <td><a href="https://github.com/MSzturc/t100/blob/main/STL/Top%20Frame/Connection%20Side%201.stl">Connection Side 1</a></td>
      <td><a href="https://files.printables.com/media/prints/430339/stls/3564405_5d425572-0da8-4a00-8df0-95a4e943c9a5/top-connector-side-1.stl">Top Connector Side 1</a></td>
      <td>4</td>
      <td><a href="#top-connector-side-1">More info</a></td>
    </tr>
    <tr>
      <td><a href="https://github.com/MSzturc/t100/blob/main/STL/Top%20Frame/Connection%20Side%202.stl">Connection Side 2</a></td>
      <td><a href="https://files.printables.com/media/prints/430339/stls/3564408_42dada54-5699-4778-8489-f2a1cf6e4681/top-connector-side-2.stl">Top Connector Side 2</a></td>
      <td>4</td>
      <td><a href="#top-connector-side-2">More info</a></td>
    </tr>
    <tr>
      <td><a href="https://github.com/MSzturc/t100/blob/main/STL/Top%20Frame/RodHolder.stl">RodHolder</a></td>
      <td><a href="https://files.printables.com/media/prints/430339/stls/3564392_4cd4773d-97a5-44f3-8adc-8ec6a5f399d0/top-rod-holder.stl">Top Rod Holder</a></td>
      <td>2</td>
      <td><a href="#top-rod-holder">More info</a></td>
    </tr>
    <tr>
      <td><a href="https://github.com/MSzturc/t100/blob/main/STL/Top%20Frame/Top%201.stl">Top 1</a></td>
      <td><a href="https://files.printables.com/media/prints/430339/stls/3564407_4ed66338-69f7-4bd8-8858-80af97338baf/top-back-left.stl">Top Back-Left</a></td>
      <td>1</td>
      <td><a href="#top-back-left">More info</a></td>
    </tr>
    <tr>
      <td><a href="https://github.com/MSzturc/t100/blob/main/STL/Top%20Frame/Top%202.stl">Top 2</a></td>
      <td><a href="https://files.printables.com/media/prints/430339/stls/3564424_8661f5e9-837a-49df-92e6-aa714adf748f/top-back-right.stl">Top Back-Right</a></td>
      <td>1</td>
      <td><a href="#top-back-right">More info</a></td>
    </tr>
    <tr>
      <td><a href="https://github.com/MSzturc/t100/blob/main/STL/Top%20Frame/Top%203.stl">Top 3</a></td>
      <td><a href="https://files.printables.com/media/prints/430339/stls/3564406_c8453471-ca49-43b2-92ea-2808661a3bc1/top-front-left.stl">Top Front-Left</a></td>
      <td>1</td>
      <td><a href="#top-front-left">More info</a></td>
    </tr>
    <tr>
      <td><a href="https://github.com/MSzturc/t100/blob/main/STL/Top%20Frame/Top%204.stl">Top 4</a></td>
      <td><a href="https://files.printables.com/media/prints/430339/stls/3564403_9b4173cf-4c82-41aa-97dc-27d2593f87ac/top-front-right.stl">Top Front-Right</a></td>
      <td>1</td>
      <td><a href="#top-front-right">More info</a></td>
    </tr>
  </tbody>
</table>

### More Info

#### Belt Fastener 

##### Printing details
  - Qty: 2
  - Filament (length/weight): 2.7m / 8.2g
  - Supports: No

  

##### Notes
None

#### Top Connector Back 1

##### Printing details
  - Qty: 1
  - Filament (length/weight): 4.7m/ 14g
  - Supports: 

  

##### Notes
None

#### Top Connector Back 2

##### Printing details
  - Qty: 1
  - Filament (length/weight): 4.3m / 12.7g
  - Supports: No

  

##### Notes
None

#### Top Connector Top 1

##### Printing details
  - Qty: 1
  - Filament (length/weight): 9.1m / 27.2g
  - Supports: No

  

##### Notes
None

#### Top Connector Top 2

##### Printing details
  - Qty: 1
  - Filament (length/weight): 9.1m / 27.2g
  - Supports: No

  

##### Notes
None

#### Top Connector Side 1

##### Printing details
  - Qty: 4
  - Filament (length/weight): 6.7m / 20.1g
  - Supports: No

  

##### Notes
None

#### Top Connector Side 2

##### Printing details
  - Qty: 4
  - Filament (length/weight): 3.9m / 11.6g
  - Supports: No

  

##### Notes
None

#### Top Rod Holder

##### Printing details
  - Qty: 2
  - Filament (length/weight): 1.9m / 5.6g
  - Supports: Yes

  

##### Notes
Supports in the screw holes touching the build plate.

#### Top Back-Left

##### Printing details
  - Qty: 1
  - Filament (length/weight): 104m / 310g
  - Supports: Yes

  

##### Notes
You may be able to print this without supports if your printer can bridge over the square where the motor goes. I recommend printing this piece with a brim to prevent warping. 

#### Top Back-Right

##### Printing details
  - Qty: 1
  - Filament (length/weight): 104m / 310g
  - Supports: Yes

  

##### Notes
You may be able to print this without supports if your printer can bridge over the square where the motor goes. I recommend printing this piece with a brim to prevent warping. 

#### Top Front-Left

##### Printing details
  - Qty: 1
  - Filament (length/weight): 91.2m / 272g
  - Supports: Yes

  

##### Notes
The only support needed is a single screw hole that touches the build plate. I recommend printing this piece with a brim to prevent warping. 

#### Top Front-Right

##### Printing details
  - Qty: 1
  - Filament (length/weight): 91.2m / 272g
  - Supports: 

  

##### Notes
The only support needed is a single screw hole that touches the build plate. I recommend printing this piece with a brim to prevent warping.

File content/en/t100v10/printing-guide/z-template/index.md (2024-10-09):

---
title: "Template"
description: ""
lead: ""
date: 2023-06-18T14:41:39+01:00
lastmod: 2023-06-21T00:41:39+01:00
draft: true
images: []
type: docs
menu:
  t100v10:
    parent: "printing-guide-the100"
weight: 999
toc: true
doc: t100v10
aliases:
  - /t100/printing-guide/z-template/
---
# Template
Everything you need to print for THE 100 top frame.

## v1.0

### Parts list

<table class="table table-sm">
  <thead>
    <tr>
      <th scope="col">GitHub</th>
      <th scope="col">Printables</th>
      <th scope="col">Qty</th>
      <th scope="col">Notes</th>
    </tr>
  </thead>
  <tbody>
    <tr>
      <td></td>
      <td></td>
      <td>1</td>
      <td>More info</td>
    </tr>
  </tbody>
</table>

### More Info

#### Part 1

##### Printing details
  - Qty: 1
  - Filament (length/weight): 
  - Supports: 

##### Notes
None

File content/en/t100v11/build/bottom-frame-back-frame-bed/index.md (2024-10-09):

---
title: "Bottom & back frames & bed build"
ogTitle: "Bottom & Back Frame & Bed Build - THE 100 Build Guide"
description: "How to build THE 100's v1.1 bottom frame, back frame, & gantry"
lead: ""
date: 2023-08-14T14:41:39+01:00
draft: false
images: []
type: docs
menu:
  t100v11:
    parent: "build-v11"
weight: 520
toc: true
doc: t100v11
images: 
  - images/tfd_bottom_frame_preview.png
---
# Bottom and Back Frames & Bed

After completing this step you will have the entire frame of the printer complete! There is still plenty of work to go with the electronics, but this is nearly the end of the physical build. The back frame is one of the primary changes between v1.0 and v1.1. 

Visit the following print & purchase guides to see what you will need to complete this part of the build: 
  - <a href="/t100/1.1/printing-guide/bottom-frame/">bottom frame</a>
  - <a href="/t100/1.1/printing-guide/back-frame/">back frame</a>
  - <a href="/t100/1.1/printing-guide/bed/">bed</a>

Then you should watch <a href="https://www.youtube.com/watch?v=EwaCh9CHoCc" target="_blank">Matt's video</a> for building the bottom frame (which includes the back frame and bed). This guide will simply function as a supplement to that video. 

## Notes on the video
The build video for the bottom frame is great and covers all steps well.
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

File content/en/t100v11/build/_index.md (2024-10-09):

---
title: "Build"
description: ""
lead: ""
date: 2023-06-18T14:41:39+01:00
lastmod: 2023-06-21T00:41:39+01:00
draft: false
images: []
type: docs
weight: 300
menu:
  t100v11:
    identifier: "build-v11"
url: /t100/1.1/build/
---

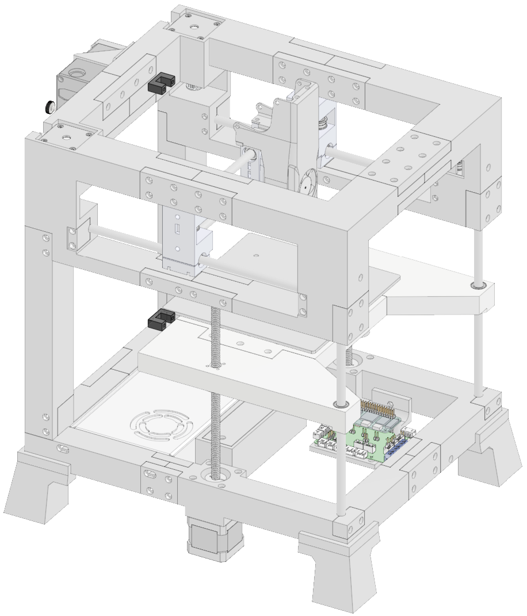
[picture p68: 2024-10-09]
content/en/t100v11/printing-guide/bottom-frame/images/cable_guides_cad.png

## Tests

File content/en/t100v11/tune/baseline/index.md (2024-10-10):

---
title: "Baseline"
ogTitle: "Get the basics configured and complete your first print! - THE 100 Build Guide"
description: "How to get THE 100 ready for its first print... and then print it!"
lead: ""
date: 2023-10-03T14:41:39+01:00
draft: false
images: []
type: docs
menu:
  t100v11:
    parent: "tune-v11"
    identifier: "baseline-tune-v11"
weight: 701
toc: true
doc: t100v11
static_images: true
images: 
  - tfd_preview_baseline.png
---
# Baseline tune
There are some fantastic printer tuning guides out there, and I have absolutely no intention of replacing them. In fact, I'll be linking to a number of them through the tuning guide with the expectation that you'll use their guides. 

To start off with, Matt (the creator of THE 100), has <a href="https://www.youtube.com/watch?v=ikvOHPZL6Cc" target="_blank">a great video on how he tunes 3d printers</a>. Matt starts his video by <a href="https://ellis3dp.com/Print-Tuning-Guide/" target="_blank">mentioning Ellis' Print Tuning Guide</a> which is the most detailed guide I've ever used. I highly recommend watching Matt's whole video and going through the entire Ellis guide. 

However... I know to get to this point you have spent weeks (or months) buying the parts, printing the pieces, assembling it all, and configuring everything. It has been a long journey and you just want to see something print already! For that reason, I'm going to focus on what I consider to be a baseline tune to where you can get something printed. 

The end result of this guide will be a printed calibration cube. This will not be the best calibration cube in existence and there will be plenty of fine tuning needed after it's printed, but it's still so exciting and motivating to finally print something! 

Now is the time.

## Requirements 
  * This guide is written with the assumption that you:
      * have followed my previous guides (the klipper/printer.cfg configuration in particular)
      * aren't using any of THE 100 mods
      * have everything built and ready to go
      * have successfully homed the printer
  
## Z endstop
The first item that requires calibrated is the Z offset. We need to know the exact distance between the nozzle and the bed when the Z endstop is triggered during the homing process. That way Klipper understands where Z=0 at. To do that we have to tell Klipper where the z endstop location is.

You can watch this process starting at <a href="https://youtu.be/ikvOHPZL6Cc?si=AI9MRj8QcVVIyNHO&t=138" target="_blank">2:18 in Matt's video</a>.

  1. Tighten your bed screws down and then loosen them all several turns. This gives us flexibility for bed leveling in the next step. 
  1. Home the printer
  1. Send the printer to location 80,80
      * `G90`
      * `G1 X80 Y80 F5000`
      * It should be basically over the center of the bed
  1. Send `Z_ENDSTOP_CALIBRATE` via the console
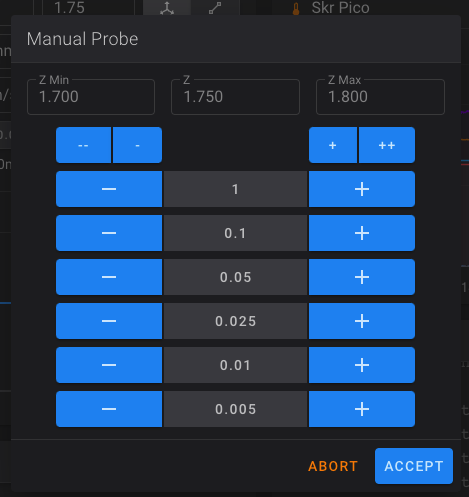
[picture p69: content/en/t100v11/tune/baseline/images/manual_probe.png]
      * 
  1. Put a piece of paper under the nozzle and then use the screen displayed in fluidd to lower the print head until it holds the paper pretty tight
      * `-` lowers the print head and `+` raises it
      * It typically starts fairly high so you will likely start by hitting `-1` a couple times to get the nozzle closer to the paper, then start using `-0.1` until you get closer, then `-0.05`.
      * Use `+` if you go too far and need to raise it
  1. Once the paper is held pretty tight, hit `Accept`
  1. Send `SAVE CONFIG` via the console. It will update your `printer.cfg` automatically for you (check the bottom of the file for the changes it made) and it will reboot for you.

<div class="alert alert-info" role="alert">
    ℹ️ 	Because this process is calculating the distance between the nozzle and the bed, you will need to repeat these steps any time you make changes to the nozzle, the bed, the gantry, etc. Anything that would impact that distance even in a little bit. 
</div>

## Bed level
Now that your Z offset is correct, we need to level the bed.

You can watch this process starting at <a href="https://youtu.be/ikvOHPZL6Cc?si=4tYndgk2fGQ5IAcu&t=200" target="_blank">3:20 in Matt's video</a> with one exception: I don't pre-tighten the screws after doing the Z endstop calibration like he did. Either way works though. 

  1. Home the printer
  1. Send `BED_SCREWS_ADJUST` via the console
      * This will send the nozzle to above the front left screw and move it to Z=0. It then displays a window for you to interact with in fluidd. 
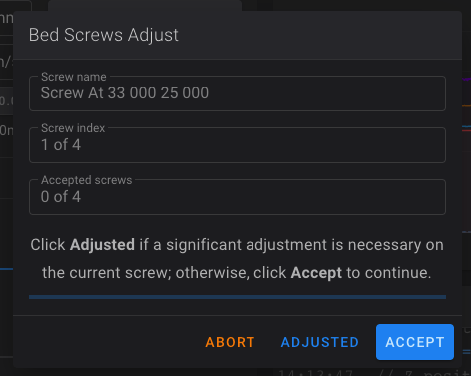
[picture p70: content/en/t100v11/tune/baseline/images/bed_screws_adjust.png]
      * 
  1. Starting with the front left screw, use <a href="https://www.klipper3d.org/Bed_Level.html#the-paper-test" target="_blank">the paper test</a> to determine if you should tighten or loosen the screw. 
      * As you go through each screw you will either hit `Adjusted` if you had to make significant changes to the screw, or `Accept` if you didn't. If you do `Adjusted` then it will come back to that screw after it goes through the other 3. I highly recommend you select `Adjusted` for all 4 screws on your first pass. It's very likely you will need to do 2, 3, 4, or more passes on your first setup before you get it level. Once you're no longer having to change much on the screw, start hitting `Accept`.
      * You will very likely have to 
  * Will need to loosen other screws at first to get the bed to raise

After leveling the bed, it's recommended to <a href="/t100/1.1/tune/baseline/#z-endstop">repeat the Z endstop calibration again</a> as the position of your bed has almost definitely changed.

## PID tuning
PID tuning is an automated process for Klipper to learn how quickly your hotend and bed heat up. This is important so that it can minimize the under and overshooting it goes through when trying to get to the set temperature. Luckily this process is complete automated. 

You can read more about this process in <a href="https://www.klipper3d.org/Config_checks.html?h=pid#calibrate-pid-settings" target="_blank">the Klipper docs</a>. 

You can watch this process starting at <a href="https://youtu.be/ikvOHPZL6Cc?si=EiVLahYs7sb0sZQL&t=270" target="_blank">4:30 in Matt's video</a> 

### Bed
Run `PID_CALIBRATE HEATER=heater_bed TARGET=60` from the fluidd console and wait for it to complete. Then run `SAVE_CONFIG`. 

### Hot end
Run `PID_CALIBRATE HEATER=extruder TARGET=200` from the fluidd console and wait for it to complete. Then run `SAVE_CONFIG`. 

After completing both and saving them, you will see new values at the bottom of your `printer.cfg` that have been automatically added. 

If you swap out any components related to your heated bed or hotend -- anything that changes how they heat up or cool down -- you'll want to redo PID tuning. But standard changes don't require it. 

## E-Steps
Calibrating e-steps is the process of confirming that your extruder motor moves the same amount of filament that it's told to. Meaning if it should deliver 100mm, it actually does. 

I have used various methods of doing this, but Matt's process starting at <a href="https://youtu.be/ikvOHPZL6Cc?si=CzaSCsX20_koA0QG&t=465" target="_blank">7:45 in his video</a> is so simple. I highly recommend it. I describe the steps in a bit more detail than Matt does, but I recommend watching how he does it so the taping and measuring makes sense. 

  1. Manually feed filament through your extruder and bowden tube until it reaches the hotend and can't go further (your hotend should not be heated up for this).
  1. Run the following commands to ensure the extruder motor is engaged
      * `G91`
      * `G1 E-1 F60`
  1. Put a piece of tape directly below the extruder where the filament comes out. This will be used as the starting point for our measurement later. 
  1. Run `G1 E-100 F60` to retract 100mm of filament
  1. Once it has completed retracting, put another piece of tape on the filament at the bottom of the extruder
  1. Manually remove the filament from your extruder so you can lay it flat
  1. Measure the distance between the right side of each piece of tape to confirm it retracted 100mm as expected.
      * If it's 100mm, you're all set!
      * If it's off then you need to calculate a new `rotation_distance`

#### Calculate rotation distance
Only do this if you didn't get 100mm as expected.

  1. Find the `[extruder]` section in your printer.cfg. Note your current `rotation_distance`.
  1. Calculate your new `rotation_distance` using this formula:
      * <new_rotation_distance> = <previous_rotation_distance> * ( <actual_extrude_distance> / 100 )
      * Note: `actual_extrude_distance` in this formula is the amount you measured that your extruder actually retracted in the previous step. 
  1. Update `rotation_distance` under the `[extruder]` section. Save & Restart. 
  1. Repeat the process above to confirm you get 100mm.

## Add printing macros
Add the following macros to your `printer.cfg`. These tell the printer what to do to start, end, or cancel a print. For organization purposes I recommend putting them below the `[gcode_macro M80]` macro. 

Note that your cfg will now have a line at the bottom that reads `#*# DO NOT EDIT THIS BLOCK OR BELOW. The contents are auto-generated.`. The items below that line were added automatically from the steps above. Hopefully it's obvious but I'll say it anyways: don't add anything below that. 

```
[gcode_macro START_PRINT]
gcode:
   {% set BED_TEMP = params.BED|default(60)|int %}
   {% set EXTRUDER_TEMP = params.HOTEND|default(200)|int %}
   CLEAR_PAUSE

   {% if printer.heater_bed.temperature < (BED_TEMP-10) %}
      M140 S{BED_TEMP-10}
   {% endif %}

   G90 ; use absolute coordinates
   G92 E0 ; reset extruder
   
   {% if "xyz" not in printer.toolhead.homed_axes %}
      G28 ; home all axis
   {% endif %}
   G1 ; set units to millimeters

   {% if printer.heater_bed.temperature < (BED_TEMP-10) %}
      M190 S{BED_TEMP-10}
   {% endif %}

   M104 S{EXTRUDER_TEMP}
   M190 S{BED_TEMP}
   M109 S{EXTRUDER_TEMP}
   DRAW_LINE SPEED=1200

[gcode_macro CANCEL_PRINT]
rename_existing: BASE_CANCEL_PRINT
gcode:
   M220 S100 ; Reset Speed factor override percentage to default (100%)
   M221 S100 ; Reset Extrude factor override percentage to default (100%)
   G91 ; Set coordinates to relative
   {% if printer.extruder.temperature >= 170 %}
      G1 F1800 E-1 ; Retract filament 3 mm to prevent oozing
   {% endif %}
   ;if all axis are homed, lift the hotend to leave room for hot filament to ooze and to keep it clear of the bed.
   {% if printer.toolhead.homed_axes == "xyz" %}
      G1 F1200 Z20 ; Move Z Axis up 10 mm to allow filament ooze freely
      G90 ; Set coordinates to absolute
      G1 X{ printer.toolhead.axis_minimum.x +10 } Y{ printer.toolhead.axis_maximum.y - 20 } F3600 ; Move Printer Head Out of Way
      ; M84 ; Disable stepper motors - don't so the gantry stays aligned
   {% endif %}
   ;set part fan speed to zero.
   M106 S0
   ;bed and hotend are left at the print temps in case I want to restart.
   CLEAR_PAUSE
   BASE_CANCEL_PRINT

[gcode_macro END_PRINT]
gcode:

    # Move nozzle away from print while retracting
    G91 ;releative positioning
    G1 E-1 F2700 ;Retract a bit
    G1 E-1 Z0.2 F2400 ;Retract and raise Z
    G1 X-3 Y-3 F3000 ;Wipe out
    G1 Z10 F400 ;Raise Z more

    # Turn off bed, extruder, and fan
    M140 S0
    M104 S0
    M106 S0

    G90 ; Absolute Positioning
    G1 X{ printer.toolhead.axis_minimum.x +10 } Y{ printer.toolhead.axis_maximum.y - 20 } F3600 ; Move Printer Head Out of Way

    M84 X Y E ;Disable all steppers but Z

[gcode_macro DRAW_LINE]
gcode:
    {% set SPEED = params.SPEED|default(900)|int %}
    G92 E0 ;Reset Extruder
    G1 Z1.0 F400 ;Move Z Axis up

    G1 X5.1 Y140 Z0.3 F5000  ;Move to start position
    G1 X5.1 Y40.0 Z0.3 F{SPEED} E15 ;Draw the first line
    G1 X5.4 Y40.0 Z0.3 F{SPEED} ;Move to side a little
    G1 X5.4 Y140 Z0.3 F{SPEED}.0 E30 ;Draw the second line

    G92 E0 ;Reset Extruder
    G1 Z1.0 F400 ;Move Z Axis up
    G4 P500
    G1 X8 F{SPEED} ;Move to side so it doesn't crash in to the blob
```

Do `Save & Restart`.

## Print a calibration cube!
### Slice the model
  1. Download and install <a href="https://ultimaker.com/software/ultimaker-cura/#links" target="_blank">Cura 5.x</a>
  1. Add a new printer to Cura
      * Follow Matt's steps <a href="https://github.com/MSzturc/t100/blob/main/Cura/Readme.md" target="_blank">in his readme</a> to add a printer
        * Do not miss the step of adding the Start G-code and End G-code
        * You can skip his steps 4 and 5 for now
  1. Download and import <a href="https://github.com/MSzturc/t100/tree/main/Cura" target="_blank">Matt's Cura profiles</a>
      * Preferences -> Configure Cura -> Profiles -> Import
  1. Download the <a href="https://www.thingiverse.com/thing:1278865" target="_blank">calibration cube stl</a> and load it in to Cura
  1. Select `The-100-Quality-Profile` as your profile. Then slice and save the gcode. 

### Upload and print
The time has come to print! 

From fluidd: select the `Jobs` icon on the left, then `+` icon at the top right, and upload your sliced gcode. Be on standby, ready to hit Emergency Stop if anything goes wrong. Then watch, wait, and marvel at the printer you built (hopefully) printing its first model!

About 20 minutes later... done!!

<div class="alert alert-info" role="alert">
    💾 	Take a moment now to download a copy of your `printer.cfg` to your computer and rename it to include today's date, or `printer.cfg-holy_crap_it_printed` or something like that. If you end up breaking your cfg in future steps, or if your SD card gets corrupted, or anything else like that... you'll be glad you have this saved! I highly recommend repeating this process any time you make important cfg changes. 
</div>

Your first question may be: why did it take 20 minutes? Cura said 12 minutes. And I thought this thing could print a benchy in just a few minutes. Well the answer is: things were intentionally slow to prevent you from destroying your printer on the first print. 

Now that things are working, it's time to tune beyond the baseline. I recommend going through all of <a href="https://ellis3dp.com/Print-Tuning-Guide/" target="_blank">Ellis' Print Tuning Guide</a>. As you get things dialed in and you're ready to go faster, you'll need to make adjustments to your `printer.cfg` to allow it to move faster. In particular, these items at the top prevent it from going fast

```
max_velocity: 100
max_accel: 1000
max_z_velocity: 15
max_z_accel: 50
```

Good luck and have fun!

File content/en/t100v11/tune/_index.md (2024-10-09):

---
title: "Tune"
description: ""
lead: ""
date: 2023-10-03T14:41:39+01:00
lastmod: 2023-10-03T14:41:39+01:00
draft: false
images: []
type: docs
weight: 500
menu:
  t100v10:
    identifier: "tune-v11"
url: /t100/1.1/tune/
---

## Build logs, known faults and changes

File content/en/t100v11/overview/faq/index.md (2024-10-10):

---
title: "FAQ"
ogTitle: "FAQ - THE 100 3d Printer"
description: "Questions about sourcing, printing, and building THE 100 v1.1 3d printer"
lead: ""
date: 2023-07-11T14:41:39+01:00
draft: false
images: []
type: docs
menu:
  t100v11:
    parent: "overview-v11"
    identifier: "faq-v11"
weight: 90
toc: true
doc: t100v11
images: 
  - images/tfd_faq.png
---
# Frequently Asked Questions
This FAQ will include answers directly on this page, as well as provide links to other pages or other locations. I will continually update it as I see questions come up. 

## General FAQ

### What is different between v1 and v1.1?
  * New Toolhead: The toolhead was redevelop from scratch. Compared to v1.0 it's able to push about 65% more air at the critical point directly under the nozzle.
  * New Feet: The new feet are able to absorb 25%-30% more force before the frame starts shaking
  * Removed Rods from the back of the printer: This removed 2 linear rods from the BOM reducing the price of the printer by another 7-10$
  * Clearance fix for Toolhead: The toolhead is now able to move 5-6mm more in the X-Axis
  * Added allen wrench holes for X/Y-Motors
  * Added Nut-Inserts to the Mainboard Mount
  * Added Clamp to fix Power Cord
  * Made LM8UU Exchangable
  * Added Quickmounts for Z-Rods
  * Bugfix: Power Supply Holder
  * Added cable guides for proper cable management

<a href="https://discord.com/channels/1086229147107459133/1086242902193225748/1117775589454135337" target="_blank">Source</a>

### Should I make v1, v1.1, or wait for v2?
I would highly recommend printing v1.1 rather than v1 due to the various quality of life upgrades and fixes that come with v1.1. Note that there are several part differences between the two so you'll need to make sure and print the correct parts for v1.1.  

v2, which is currently planned for March 2024, is pretty much going to be a different printer with major design changes. Matt has said there will be a direct drive toolhead and I've seen mention of potentially having 4wd (4 motors for X/Y movement). I wouldn't recommend waiting for v2; I would definitely go for v1.1. 

<a href="https://discord.com/channels/1086229147107459133/1086242585049305150/1124699337029591080" target="_blank">Source 1</a>, <a href="https://discord.com/channels/1086229147107459133/1086242585049305150/1138111012462145598" target="_blank">Source 2</a>, <a href="https://discord.com/channels/1086229147107459133/1086240900520345650/1118305868476338247" target="_blank">Source 3</a>

### What is the bed size?
THE 100 uses a 165*165 bed size -- the BOM recommends using an Ender 2 Pro bed. 

### Can I use a larger bed size?
Matt specifically chose 165*165 as the sweet spot between being large enough, and speed. Increasing the bed size will slow the printer down which isn't the goal of THE 100. 

However, there are several 235*235 created by the community <a href="https://discord.com/channels/1086229147107459133/1086248812219224125" target="_blank">in the mods section</a>. For example: one by <a href="https://discord.com/channels/1086229147107459133/1088227946596147221" target="_blank">btlucas</a>, and another by <a href="https://discord.com/channels/1086229147107459133/1093732964631842836" target="_blank">Duncan</a>. 

<a href="https://discord.com/channels/1086229147107459133/1086242585049305150/1138111893211459615" target="_blank">Source</a>

## Printing FAQ
### Why use PLA / Can I print with some other filament?
Despite what most people think, PLA is extremely rigid. And when you're printing a frame that needs to be stiff... you want a rigid filament. Other filaments (like PLA+) may be "stronger" because they're more flexible and can bend without breaking, but bending isn't a good quality in what should be a rigid frame. PLA also has good dampening properties and creates a consistent vibration profile.

Other filaments, like ABS, will work but they have a lower material density than PLA so you will need to increase infill to compensate for that. ASA is another option if you need to withstand higher heat than the printer is originally designed for. 

The ultimate answer is that PLA works great for this project, and it's the most affordable, which aligns with the THE 100's goals.

<a href="https://discord.com/channels/1086229147107459133/1086242585049305150/1135687700033318962" target="_blank">Source 1</a>, <a href="https://discord.com/channels/1086229147107459133/1086240900520345650/1133912749747998772" target="_blank">Source 2</a>, <a href="https://discord.com/channels/1086229147107459133/1086242585049305150/1109794216244150363" target="_blank">Source 3</a>

### How long does it take to print THE 100?
Details on how long it takes and how much filament is used can be found <a href="https://theforgetful.dev/t100/1.1/overview/before-you-print/#print-time">in the overview</a>. 

## Buying / Sourcing FAQ
### How many fasteners (screws / heat inserts / etc) do I need?
This is the question I've seen the most and is what lead me to create this whole guide. A grand total can be found <a href="https://theforgetful.dev/t100/1.1/overview/bill-of-materials/#fasteners--hardware">here</a>, with individual counts being listed with each particular part (<a href="https://theforgetful.dev/t100/1.1/printing-guide/top-frame/#top-back-left">example</a>). 

### Can I use something other than the Ender 2 Pro bed?
I've seen several people report not being able to source the Ender 2 Pro bed. I suspect this is a country-specific issue as the vast majority find them readily available on aliexpress or directly from the Ender store. However, check <a href="https://discord.com/channels/1086229147107459133/1086248812219224125" target="_blank">the mods section</a> for various modifications that allow you to use other beds.

For example: <a href="https://discord.com/channels/1086229147107459133/1097124182883586099" target="_blank">Prusa Mini bed by cpx</a>, <a href="https://discord.com/channels/1086229147107459133/1095690631461994527" target="_blank">KP3S bed by MashedPotato</a>, and <a href="https://discord.com/channels/1086229147107459133/1095265967082328075" target="_blank">Ender 3 bed by Overgo</a>. 

### Does the SD card matter?
I <b>HIGHLY</b> you purchase a quality SD card rather than using a cheap offbrand one. Cheap flash memory <i>could</i> work fine, or it could be the source of constant gremlins that are impossible to chase down. If you find that you have things working and then suddenly they stop... the SD card is the most likely culprit. A basic 32GB SanDisk ultra can be bought for about $5 on Amazon and will save you so many headaches.

### Do I need the wifi antenna for the Banana Pi?
Yes, you definitely need the antenna. I had my BPi within 10 feet of a wifi access point and I still couldn't get internet without an antenna plugged in.

### What motors should I get?
#### The BOM motors
THE 100 BOM currently links to motors that offer 3 options: `17HS4401-XH2.54`, `17HS4401-DuPont`, and `17HS4401S-DuPont`.

`-XH2.54` and `-DuPont` simply refers to the the type of connector that comes on the end of the cable that connects to the mainboard (the SKR Pico). 

{{< thumbnail src="images/dupont-vs-xh254.png">}}

The white connector is XH2.54 and the black is DuPont. You'll notice in both cases that the cable has at least one white connector. That's because every stepper motor (at least of this type) uses XH2.54 on the motor side. You may also notice that other than the black one being deeper, the pins are spaced out the same. 

It does not matter if you get XH2.54 or DuPont as both can plug in to the same connector on the SKR Pico. The benefit of the XH2.54 is that it will give you a tighter fit that is less likely to come out, but it can only be inserted one direction. The benefit of the DuPont is you can flip it over and still insert it, which is helpful since the wiring for stepper motors isn't a standard. You can also change the connector or replace the cable very easily if you want.

For `17HS4401` vs `17HS4401S`, this again isn't a standard but in the case of the BOM motors, the `S` has some silver banding at the top and bottom while the other one is all black. 

{{< thumbnail src="images/black-vs-silver.png">}}

#### Other motors
There are countless other motors from other brands that may have identical part numbers but different specs. For example, in other cases the `S` designates the pinout order. Or the quality of the motor. Or several other things. The only thing you can really do is look at spec sheets to understand what the difference is. Ultimately it likely doesn't matter. 

The important part is that you can have a max of 38mm for the z-axis (without mods). 

I personally use StepperOnline 17HE15-1504S (for the z-axis) and 17HE19-2004S (for X/Y-axis and Extruder), but there's no reason to think they're better or worse than the ones in the BOM.

### What kind of wiring / how much wiring do I need?
The BOM calls for 2 meters of red and black wires, and the question comes up often what it's for and what size to get.

The only planned place to use those wires is to power the SKR Pico off the PSU. At the most that is 200W at 24v, and it's also a short run. Using a standard wire size calculator and inputting wire length as 30cm, the minimum wire size is 21 AWG. Honestly 30cm is longer than needed -- mine are only 20cm long which only requires 23 AWG -- but builds will vary. 

{{< thumbnail src="images/wire-awg.png">}}

With that said, I would recommend going with 18 AWG silicone insulated cables. 18 AWG is more than enough for anything you would use it for in the printer, and the silicone keeps it nice and flexible. And I would recommend going with 2 meters of each color just so you have extra in case you need it. 

<a href="https://discord.com/channels/1086229147107459133/1089229033243426896/1127250763962404914" target="_blank">Source</a>

## Building FAQ

## Software FAQ
### Which version of Armbian do I download?
Armbian 21.08.1 bananapim2zero bullseye 5.10.60 from armbian bananapim2zero archive. https://www.youtube.com/watch?v=qtmPxSt6baU @ 2:10.

Newer versions have issues to avoid.

## Tuning FAQ

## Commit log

2024-10-09 added version from TFD as base
    [back_connector.3mf, back_left.3mf, back_right.3mf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]
2024-10-10 fixed home button
